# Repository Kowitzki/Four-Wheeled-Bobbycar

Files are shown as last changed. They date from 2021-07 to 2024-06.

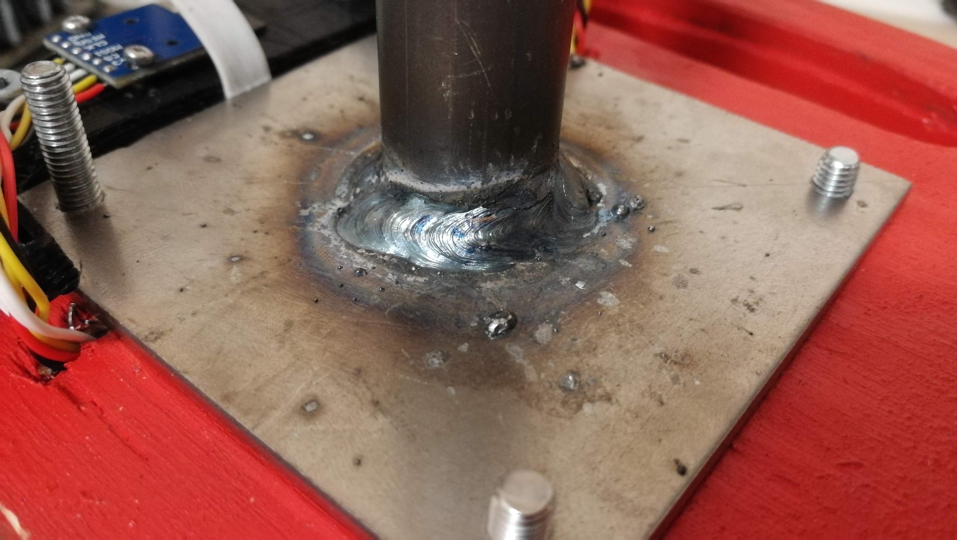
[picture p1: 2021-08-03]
Pictures/IMG_20210313_230046.jpg

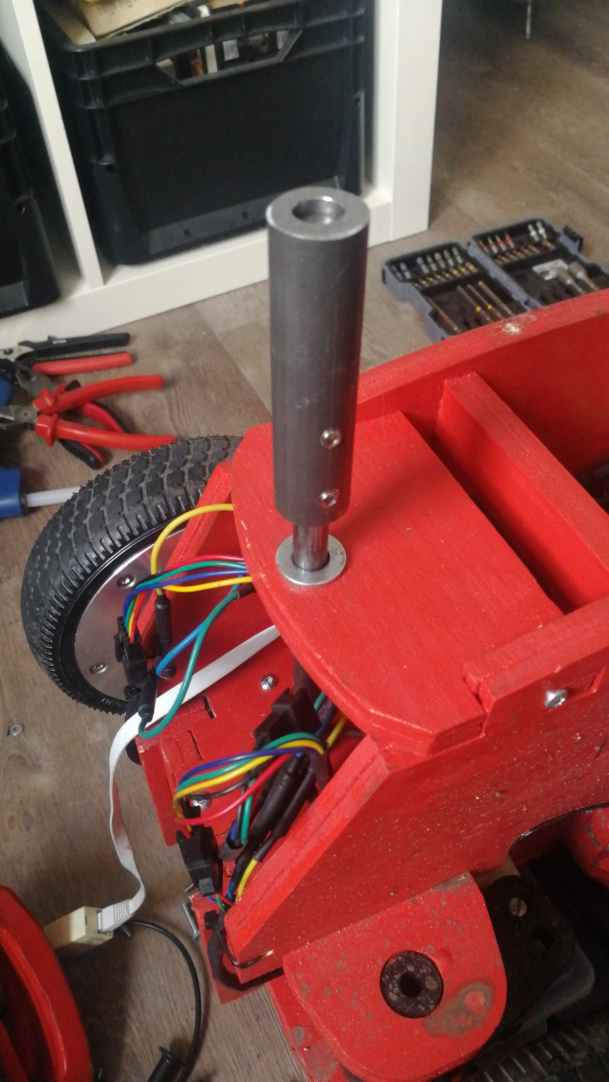
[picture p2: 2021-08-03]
Pictures/IMG-20210312-WA0000.jpeg

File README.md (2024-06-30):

# The black Bobbycar you saw at FSA 2021
There are many possible configurations to built a bobbycar like mine. So you can make changes to any part of this instruction. For example, if you want a better steering, you can change that part. Or if you do not want a Main Controller, you can use the Motorcontrollers directly connected to the potentiometers (throttle and brake).

I recommend to use Hoverboards, you get them used for ~30€ a piece, and they contain almost everything you need. This includes the Motors, which are inside the wheels, the Motorcontroller, which can drive two wheels and the accumulator.
The accumulators are pretty shitty, so not expect them to last very long. In a bobbycar they are overloaded. It helps if you put more of them in there. But you could use other types as well.

The build process gets much easier if you take the rear wheel version instead of the four wheel version. You dont have to weld and you really dont need a seperate main controller. If you are not an electronics or mechanics expert, take the rear wheel version. You find it here: https://github.com/Kowitzki/Rear-Wheeled-Bobbycar  
If you want to build something like this, keep in mind that 3kW is a lot of power and you can harm yourself or others easily. It does not have the safety a formula student car has, so please be careful at testing a new software. I highly recommend to implement a deadman switch, that ensures you really want the motors to spin.

Keep in mind, this is illegal to drive on the street in many countries.

## Software

### Motor Controller
Emanuel Feru wrote a FOC Firmware for the Hoverboard Controllers. This is the one you should flash, but you can also take the original from Niklas Fauth.

Links:
- The used Software for Inverters, took out of Hoverboards https://github.com/EmanuelFeru/hoverboard-firmware-hack-FOC
- The original Software for Inverters, took out of Hoverboards https://github.com/NiklasFauth/hoverboard-firmware-hack

My preferred IDE for the Hoverboard Software is Visual Studio Code with PlatformIO. You have to restart your PC a few times during the installation, that helped me as things did not want to appear as supposed. You can set up the config.h as you like and you can even make changes to the main.c or other files to implement new features. Keep in mind that you should not delete safety features.
Be careful in Torque Mode if you want to get more speed. The MC Software has a bug at high speed. You can drive very fast in field weakening, but then, if you let go the throttle too fast, it brakes really hard. That will not happen if you set the field weakening current in config.h to a normal value like 5-6 Ampere. IF YOU SET IT HIGHER, TELL EVERYONE WHO DRIVES ABOUT THAT ISSUE. 

### Main Control
The Main Controller is programmed by the Arduino IDE with STM32duino. I will upload the software for that but wont go into detail. Maybe i will add some comments.

ST-Link:
You should use a ST-Link V2 for programming the Motor Controllers and the Main Controller.
- ST-Link V2 https://www.ebay.de/sch/i.html?_nkw=st-link+v2&_sop=12
- Virtual COM Port Drivers https://www.st.com/en/development-tools/stsw-stm32102.html

STM32 ST-Link Utility:
From factory the Hoverboard Motorcontrollers are locked, so you have to unlock them by using the STM32 ST-Link Utility and a Flash Device called ST-Link V2. To use the ST-Link you have to install the Virtual COM Port Drivers.
- STM32 ST-Link Utility https://www.st.com/en/development-tools/stsw-link004.html
- How To Unlock https://github.com/EmanuelFeru/hoverboard-firmware-hack-FOC/wiki/How-to-Unlock-MCU-Flash

## Electronics
I would say the electronics of my Bobbycar are pretty advanced, i can control the settings via bluetooth, i have Torque Shifting and a brake light. I would recommend you to not implement those features until it drives. Otherwise you could run into a few problems. These are the parts i used just so this instruction is complete. It would be far easier to take an arduino nano and two potentiometers and flash the arduino code you find in the repository here: https://github.com/EmanuelFeru/hoverboard-firmware-hack-FOC/tree/master/Arduino/hoverserial.

Parts:
- 2x Hoverboards
- 2x 13s eBike Battery with BMS
- Potentiometers out of old XBox360 Controller
- STM32F4 Black Pill (STM32F1 Blue Pill should also work but with another pin configuration)
- Bluetooth HC05
- Display 1602 LCD
- Steering Sensor AS5600
- XL7015 DCDC Converter
- 1x N Mosfet (over 60V V_DS, whatever is lying around, like 110N8F6)
- 1x P Mosfet (over 60V V_SD, whatever is lying around, like IRF9530N)
- 2x Diode
- 2x 10k Resistor
- 1x 50k Resistor
- Port Expander PCF8574A

Schematic for Electronics: https://github.com/Kowitzki/Four-Wheeled-Bobbycar/blob/main/SchematicFourWheel.png

Accumulator
I used two ebike accumulators from aliexpress. They have more voltage than those from Hoverboards, which means a higher speed. Also they have more capacity. Till now they last far better than the original ones.
Two of them have a capacity of about 550Wh, which lasts for 40km at about 20kmh and much coasting without braking.

Links:
- The Schematic of the Hoverboard Controllers https://beta.ivc.no/wiki/images/d/d7/Hoverboard_schematic_full_reverse.pdf
- STM32F4 BlackPill https://docs.zephyrproject.org/latest/boards/arm/blackpill_f411ce/doc/index.html
- STM32F4 BlackPill https://stm32-base.org/boards/STM32F411CEU6-WeAct-Black-Pill-V2.0.html

## Mechanics
The provided CAD Model is built in Autodesk Inventor, but there you can also find a step export.

### Frame
The Frame is built from 6mm and 21mm Plywood (Sperrholz), the kind with long fibres, not pressboard/particle board (Pressspan). Plywood is much more rigid.
There are dxf-files under "Mechanics" for lasercutting. Cutting by Hand is also possible, therefor you need an A3 printer and a jigsaw.
After cutting, 12mm parts are glued together out of 6mm pieces, then everything is pushed together and tightend by screws. Assembling the steering is not that easy, my bad.
If you want your wood to last longer in the rain i recommend you to paint it.

### Steering
The uprights are printed using a 0.8mm or 1mm nozzle, a layer hight of 0.3mm and 60-80% infill. There are two options for the steering, one for normal driving and one for drifting. The options have a different geometry.
Unfortunately the steering shaft has to be welded, but i think every formula student team has someone in their team who can weld. Stick welding is sufficient.
If you use normal structural steel like S235 the steering shaft can be bend easily, already happend twice to me. Maybe you consider getting a tougher steel for the shaft.

# Drift Tires
Yeah, you read it right, i built drift tires for this. Fortunately a pipe in Germany named "Kanalgrundrohr" has the right size for this and is made out of PVC. A slice of this can be glued to printed PLA parts, which are mounted to the hoverboard motors using an TPU adaptor. This has been built, but not been tested yet. I am confident that it will work.

# Formula-Student-Mini
Maybe we can establish a formula competition which is about small, extremely low cost and high powered vehicles. At my University we set up some rules. Some are for safety, some are to harmonize cars and some are for fun.
- Rules https://github.com/Kowitzki/Four-Wheel-Bobbycar/blob/main/Formula%20Student%20Mini%20-%20Rules%20V1.pdf

We have a Telegram Group for the Bobbycars, write a mail for the link

# Known Problems
- The steering is not going back to forward if you let go, and there is much friction. I already thought of putting bearings in there. Also a judge in FSA told me a spring could handle the caster problem.
- The Display is not working on the I2C Line, if the steeringsensor and the port expander for the brake light are used.
- If you have a four wheel car with two MCs, do not drive in field weakening when one controller is off. It would get more voltage than it is supposed to.

# Other Instructions for Bobbycars
- https://larsm.org/allrad-e-bobby-car/
- https://figch.de/index.php?nav=bobbycar

# Safety
- Do not charge unattended
- Do not delete safety features
- Do not drive on public streets
- Use a deadman switch for driving
- Think about what you want to do

# Beer
If you like my effort, i would appreciate if you get me a beer ;)
www.paypal.me/kowitzki/2.00

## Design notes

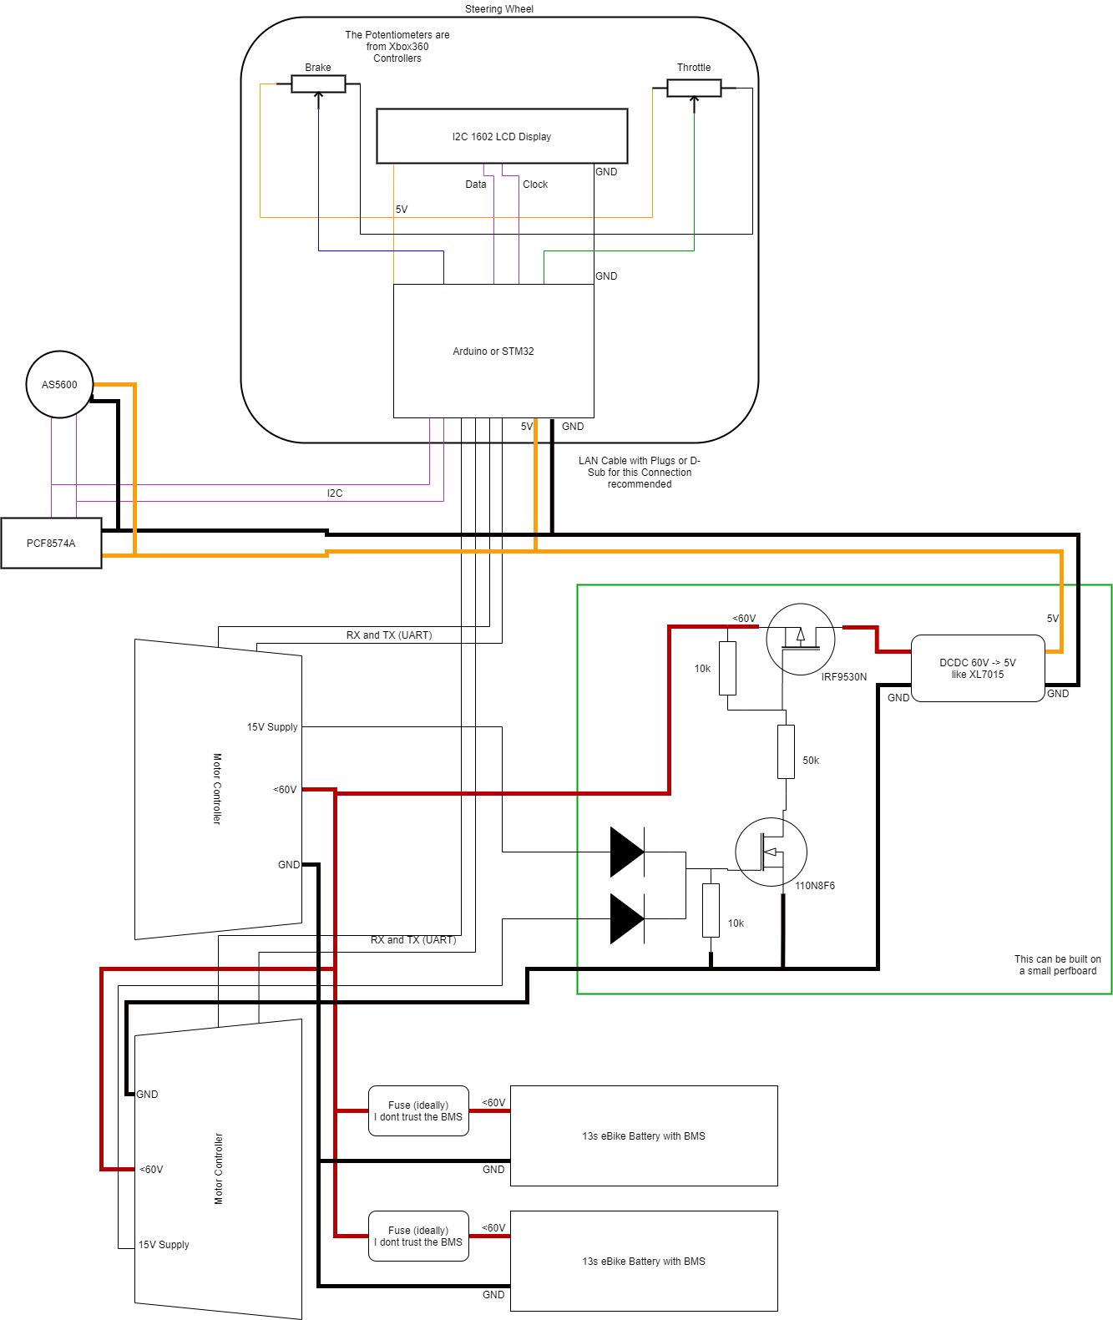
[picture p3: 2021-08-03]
SchematicFourWheel.png

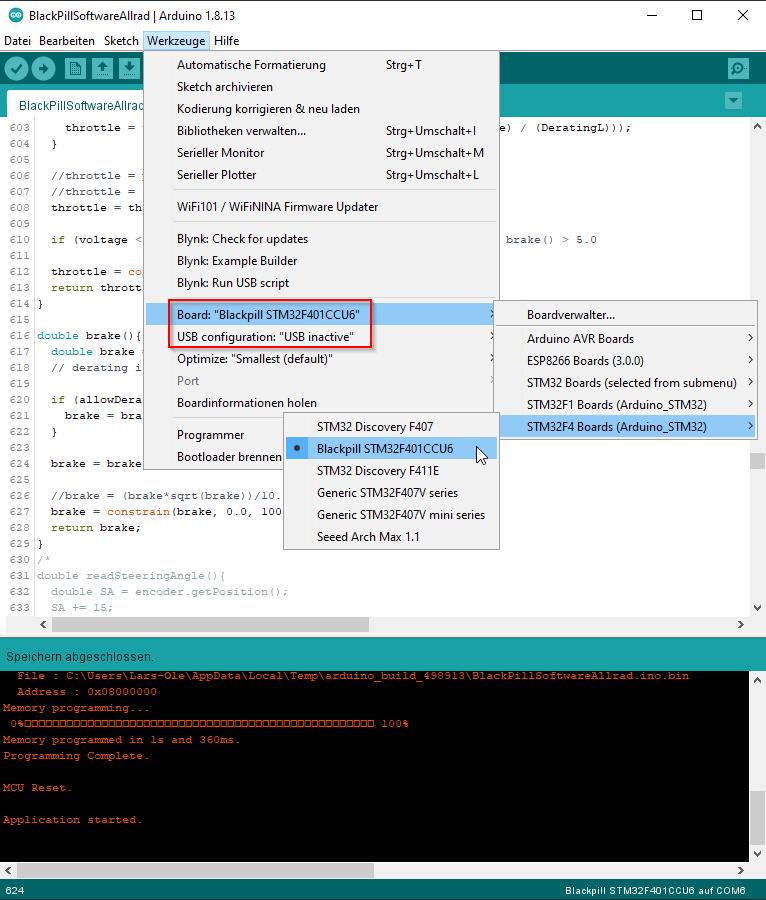
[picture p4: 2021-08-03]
Pictures/STM32_Settings.png

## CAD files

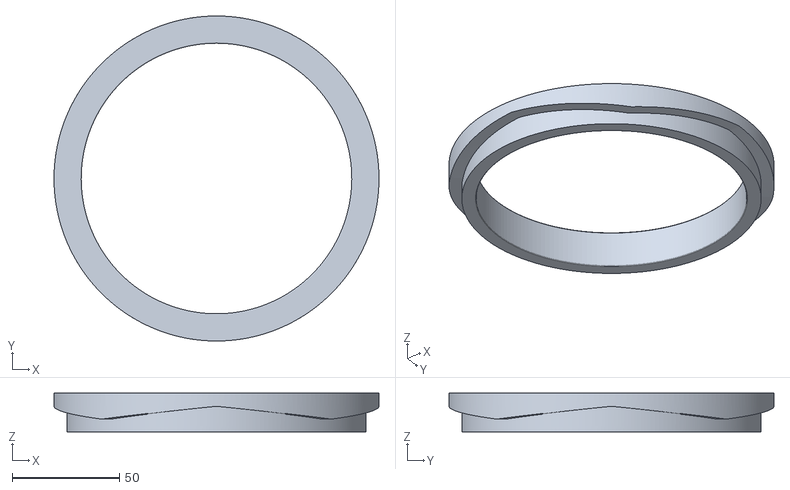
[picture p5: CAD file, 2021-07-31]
DriftreifenTPU/TPU.stl
151.9 x 151.9 x 18.2

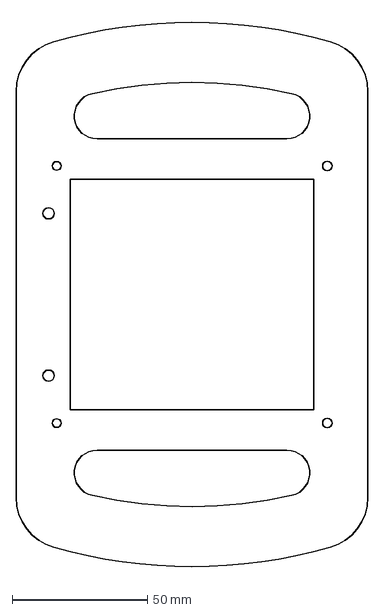
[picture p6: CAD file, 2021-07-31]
DxfWood/LenkradPlatte2.dxf
130.0 x 205.7 mm

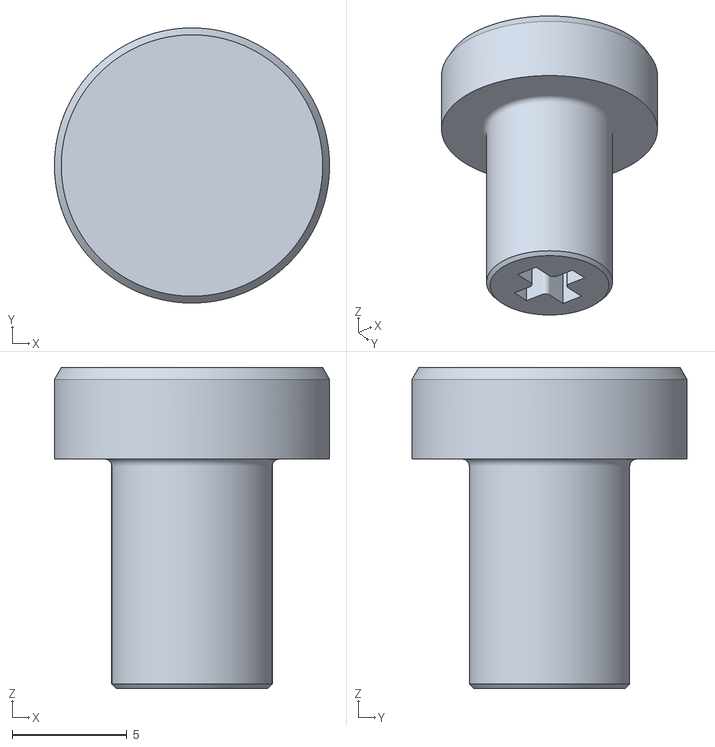
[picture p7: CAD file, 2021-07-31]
Inventor/Totmannknopf.stl
12.0 x 12.0 x 14.0

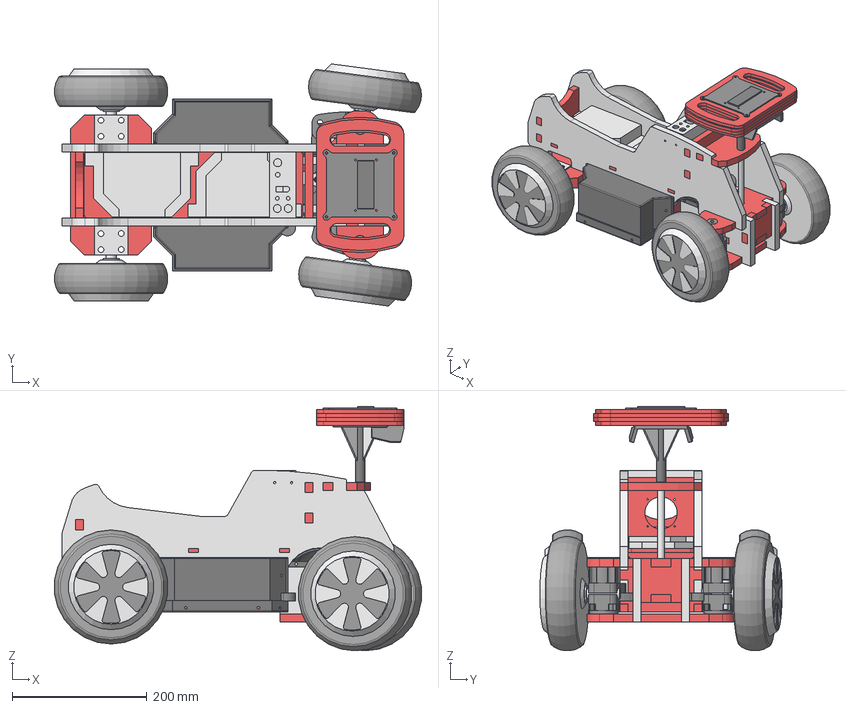
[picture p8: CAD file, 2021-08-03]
MB_BobbyCarAllrad.step
545.3 x 359.9 x 363.2 mm
Kabel
Spannbloecke
Motorplatte
Spannbleche
Haupttraeger
Controllerplatte
Akkubefestigung
QuerstrebeHinten
LenkradStahlplatte
LenkradRohr
LenkradPlatte1
LenkradPlatte2
LenkradPlatte3
LenkradPlatte4
Controller x 2
Akku13s6p
LenkungOben
AkkuSchutz
SeitenträgerInnen
Achsen x 4
Motoren x 4
LenkungUnten
RadträgerL
RadträgerR
Spurstange
SpurstangeGut
Lenkwelle
HalterungLenkwelle
DIN 427 - M8 x 25 x 3
Bodenplatte
XboxTrigger3cuttedScaled
Triggerhalter
Display
LenkradAbdeckung
MCFlashAbdeckung
LenkradStahlVersteifung
RadträgerRUnten
RadträgerLUnten
DIN 7984 - M8 x 40
QuerstrebeVorne
QuerstrebeLenkung
FührungLenkwelle
AkkuSchutzSeitlich
AkkuSchutzSeitlichR
SchutzblechVorneR
SchutzblechVorne
SchalterPanel

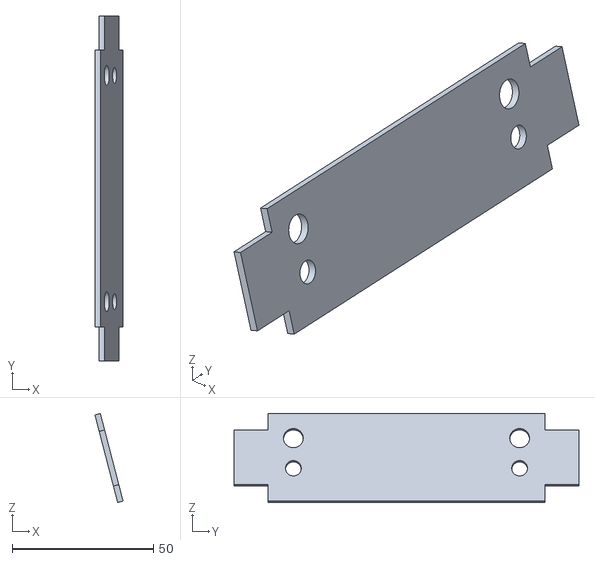
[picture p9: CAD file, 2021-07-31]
PrintedParts/MCFlashAbdeckung.stl
9.98 x 122.0 x 31.5

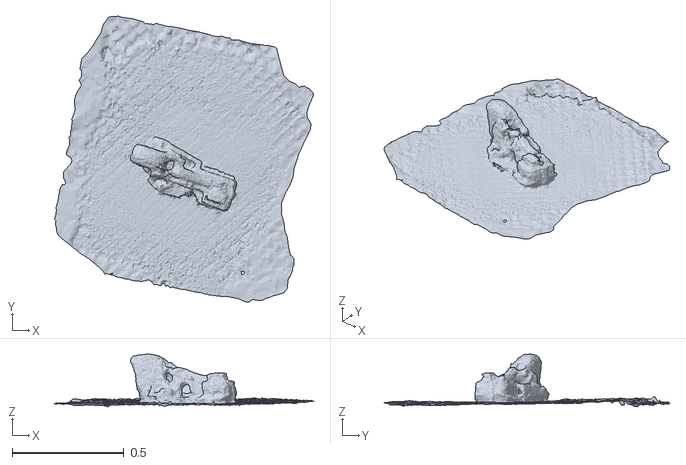
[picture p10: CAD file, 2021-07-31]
XBoxTrigger/XboxTrigger3.stl
1.16 x 1.28 x 0.237

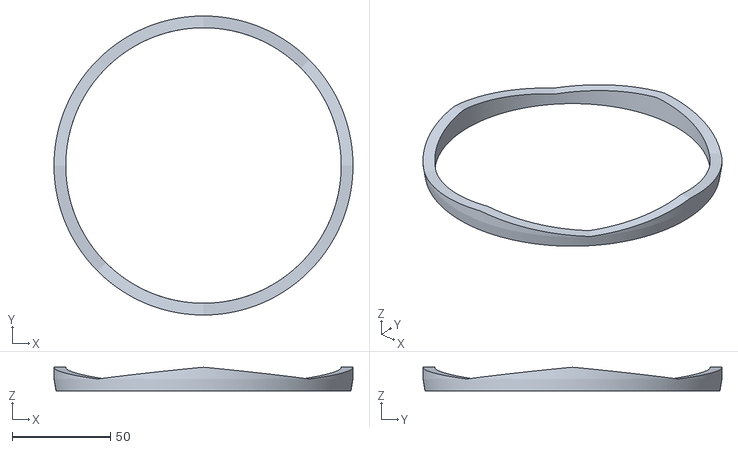
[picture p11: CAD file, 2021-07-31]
DriftreifenTPU/KlebeteiPVC.stl
152.0 x 152.0 x 12.0

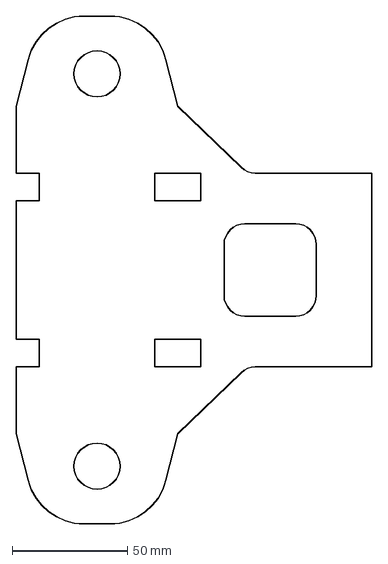
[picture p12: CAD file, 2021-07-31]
DxfWood/LenkungUnten.dxf
154.0 x 220.0 mm

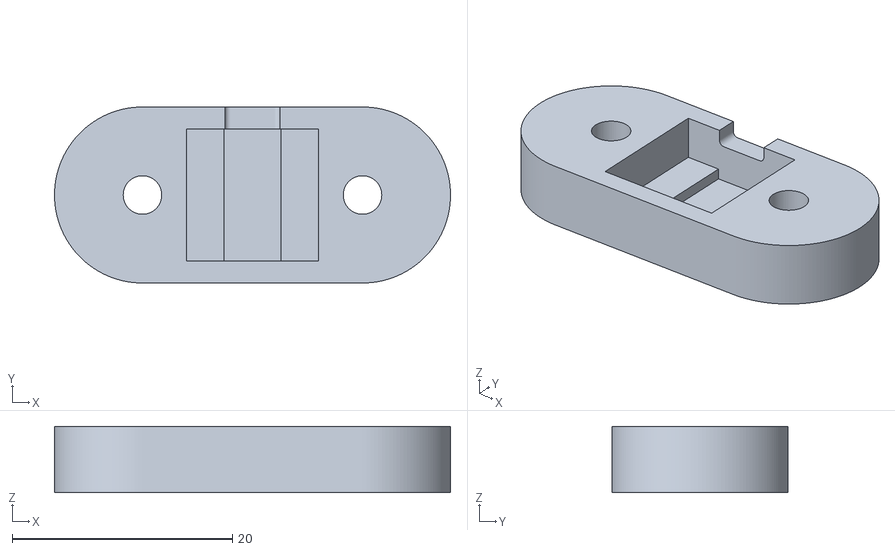
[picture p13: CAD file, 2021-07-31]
Inventor/LenkwinkelsensorAS5600.stl
36.0 x 16.0 x 6.00

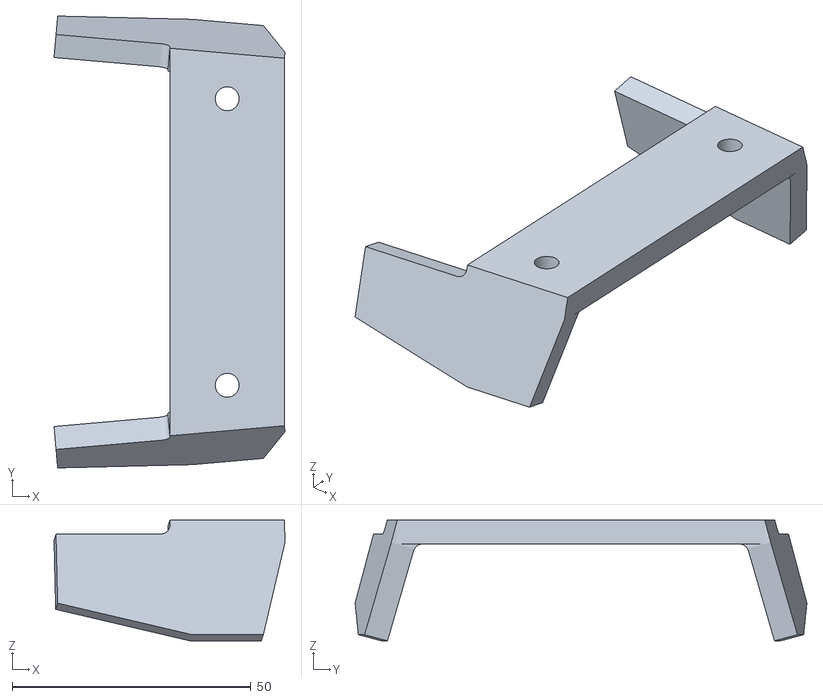
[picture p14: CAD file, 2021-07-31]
PrintedParts/Triggerhalter.stl
48.4 x 94.6 x 25.3

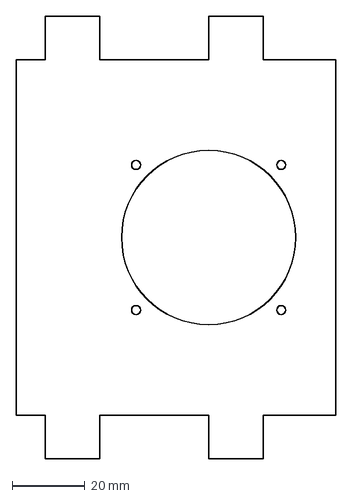
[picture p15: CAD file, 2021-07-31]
DxfWood/QuerstrebeVorne.dxf
88.0 x 122.0 mm

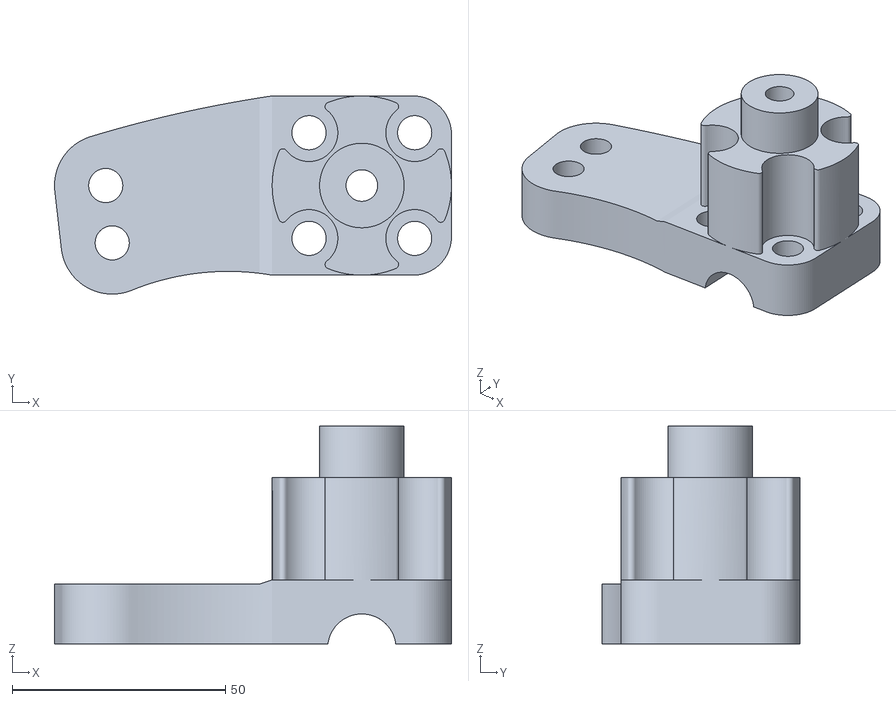
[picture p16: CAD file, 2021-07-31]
PrintedParts/RadträgerL.stl
93.0 x 46.4 x 51.0

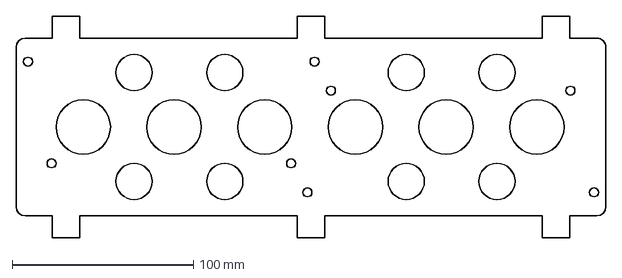
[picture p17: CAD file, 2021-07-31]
DxfWood/Controllerplatte.dxf
325.0 x 122.0 mm

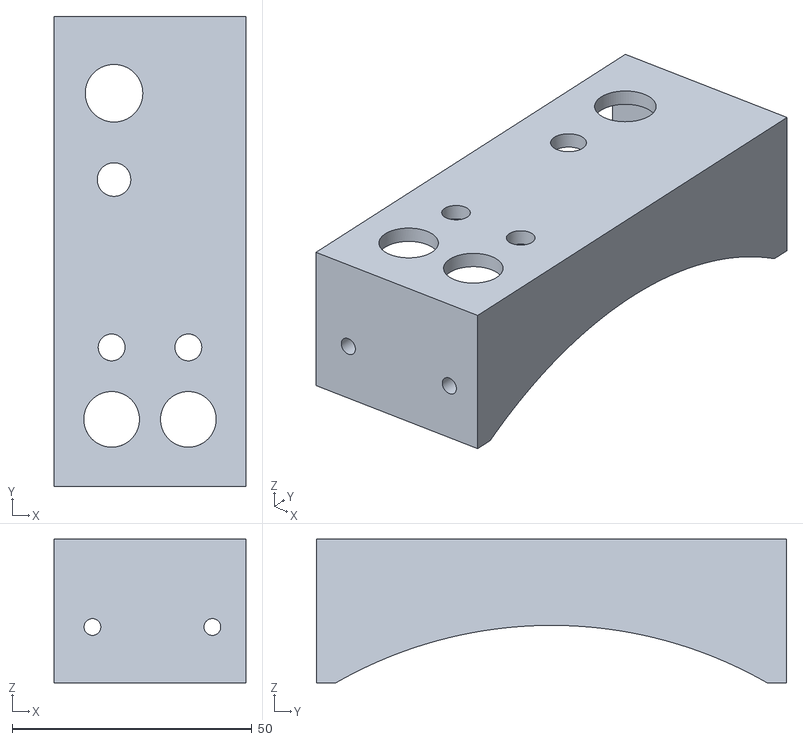
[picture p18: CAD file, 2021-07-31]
PrintedParts/SchalterPanel.stl
40.0 x 98.0 x 30.0

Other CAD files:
DxfWood/SeitentraegerInnen.dxf
PrintedParts/SchutzblechVorne.stl
DxfWood/LenkungOben.dxf
PrintedParts/AkkuSchutzSeitlich.stl
DriftreifenTPU/DriftGummisPVC.iam
DriftreifenTPU/DriftGummisPVC.ipt
DriftreifenTPU/DriftGummisPvcKlebestütze.ipt
DriftreifenTPU/KlebeteiPVC.ipt
DriftreifenTPU/PVC_Adapter.ipt
DriftreifenTPU/PVC_Adapter_Gummi.ipt
DxfWood/AkkuSchutz.dxf
DxfWood/Bodenplatte.dxf
DxfWood/FührungLenkwelle.dxf
DxfWood/HalterungLenkwelle.dxf
DxfWood/Haupttraeger.dxf
DxfWood/LenkradAbdeckung.dxf
DxfWood/LenkradPlatte1.dxf
DxfWood/LenkradPlatte3.dxf
DxfWood/LenkradPlatte4.dxf
DxfWood/MCFlashAbdeckung.dxf
DxfWood/QuerstrebeHinten.dxf
DxfWood/QuerstrebeLenkung.dxf
DxfWood/SpurstangeDrift.dxf
DxfWood/SpurstangeGut.dxf
Inventor/AchseR.ipt
Inventor/Achsen.ipt
Inventor/Akku.ipt
Inventor/Akku10s4p.ipt
Inventor/Akku12s4p.ipt
Inventor/Akku13s3p.ipt
Inventor/Akku13s6p.ipt
Inventor/AkkuSchutz.ipt
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

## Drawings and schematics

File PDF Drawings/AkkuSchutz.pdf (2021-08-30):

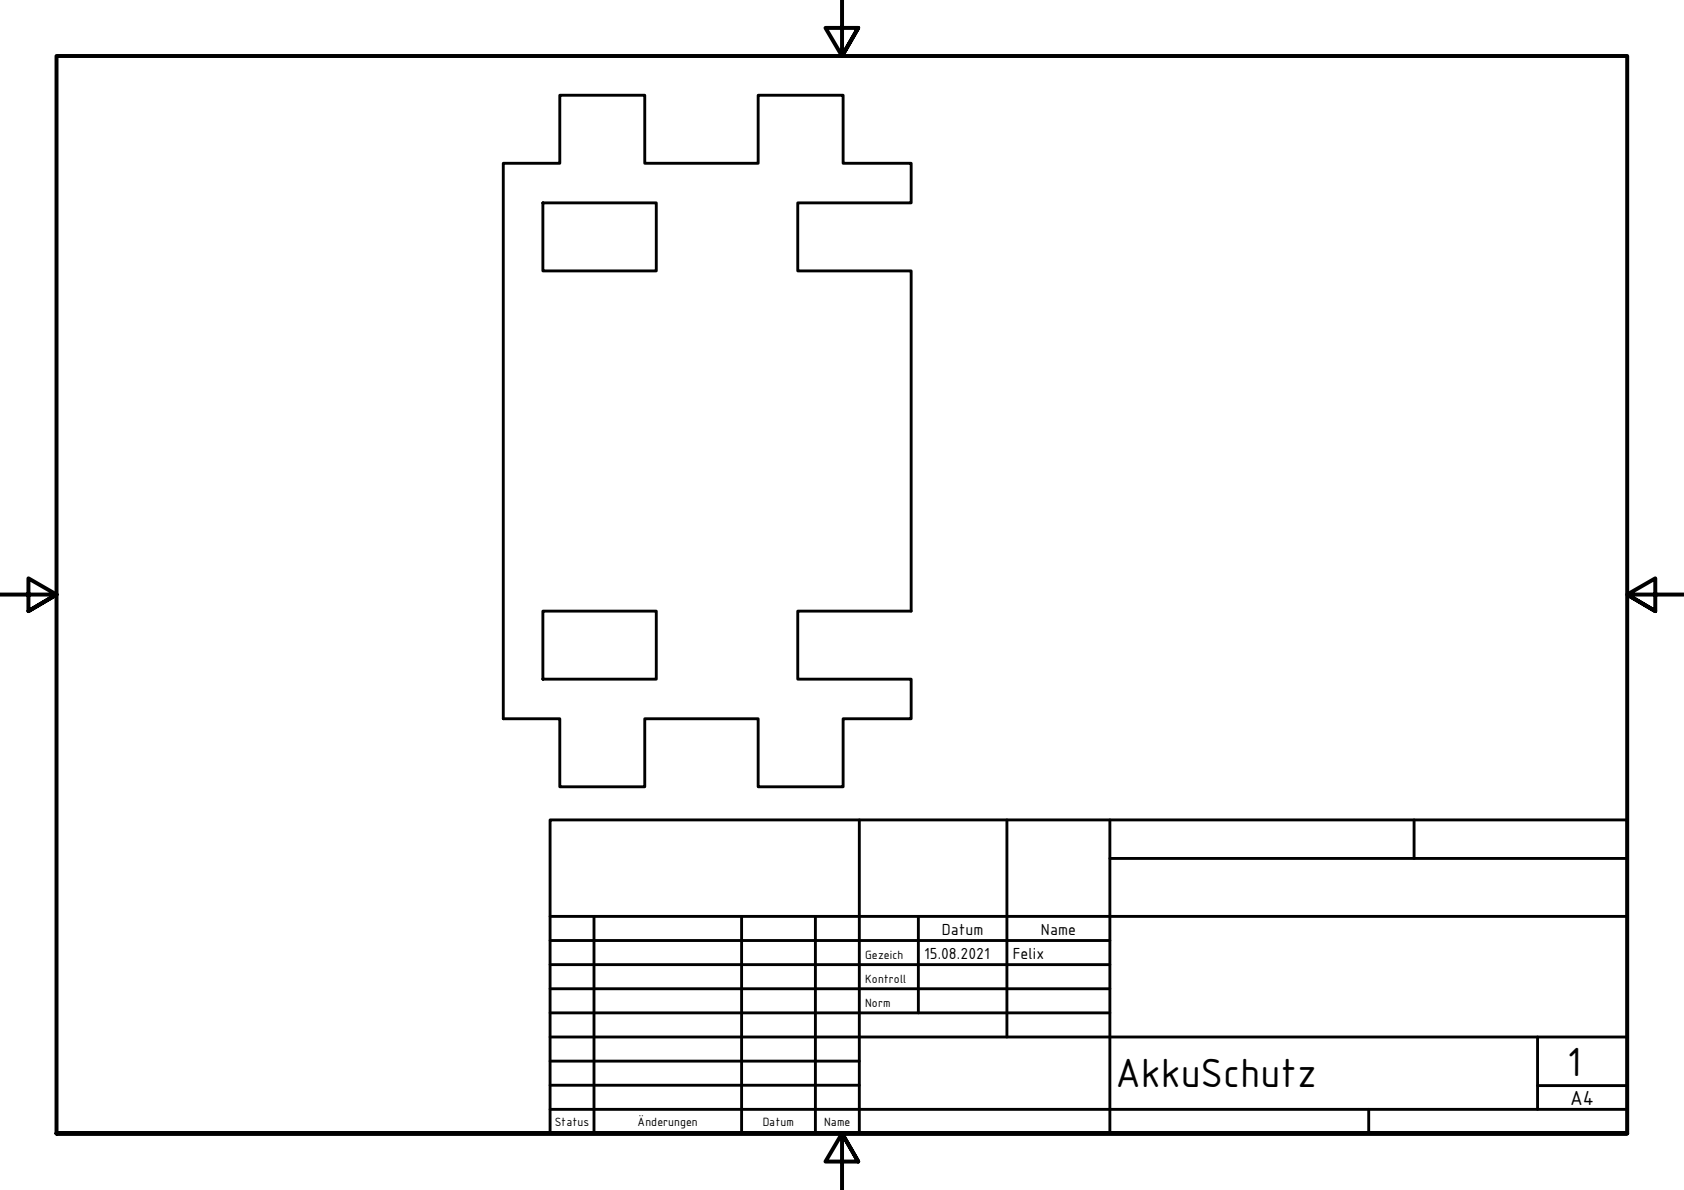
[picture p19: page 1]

G e z eic h | 1 5.0 8.2 0 2 1 | F e lix

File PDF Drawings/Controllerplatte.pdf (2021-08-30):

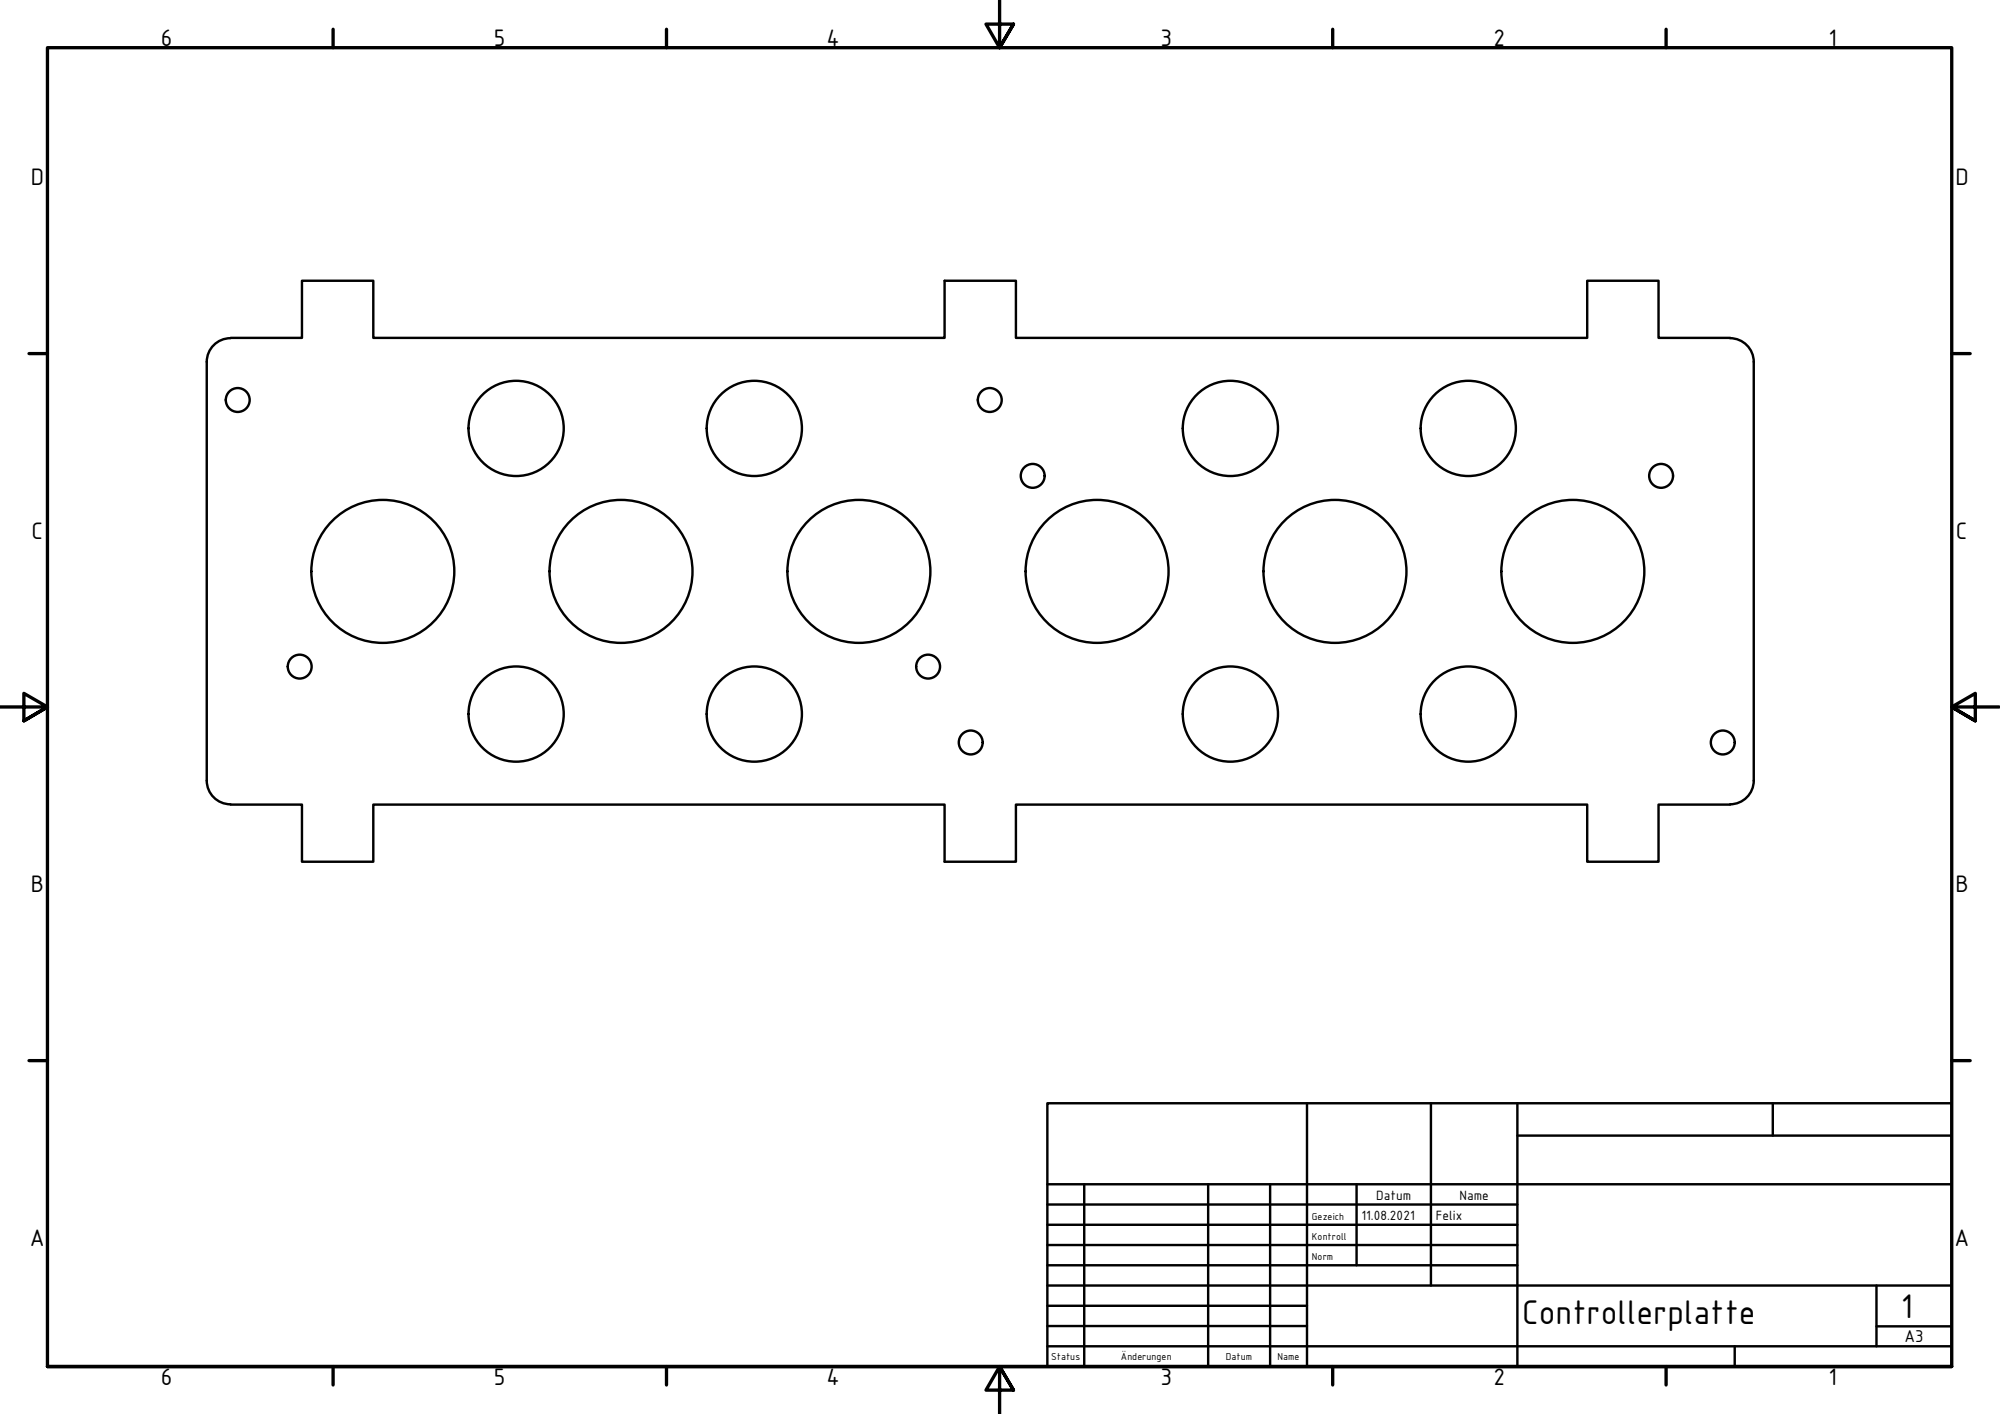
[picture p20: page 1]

Datum | Name

Gezeich | 11.08.2021 | Felix

Kontroll

Norm

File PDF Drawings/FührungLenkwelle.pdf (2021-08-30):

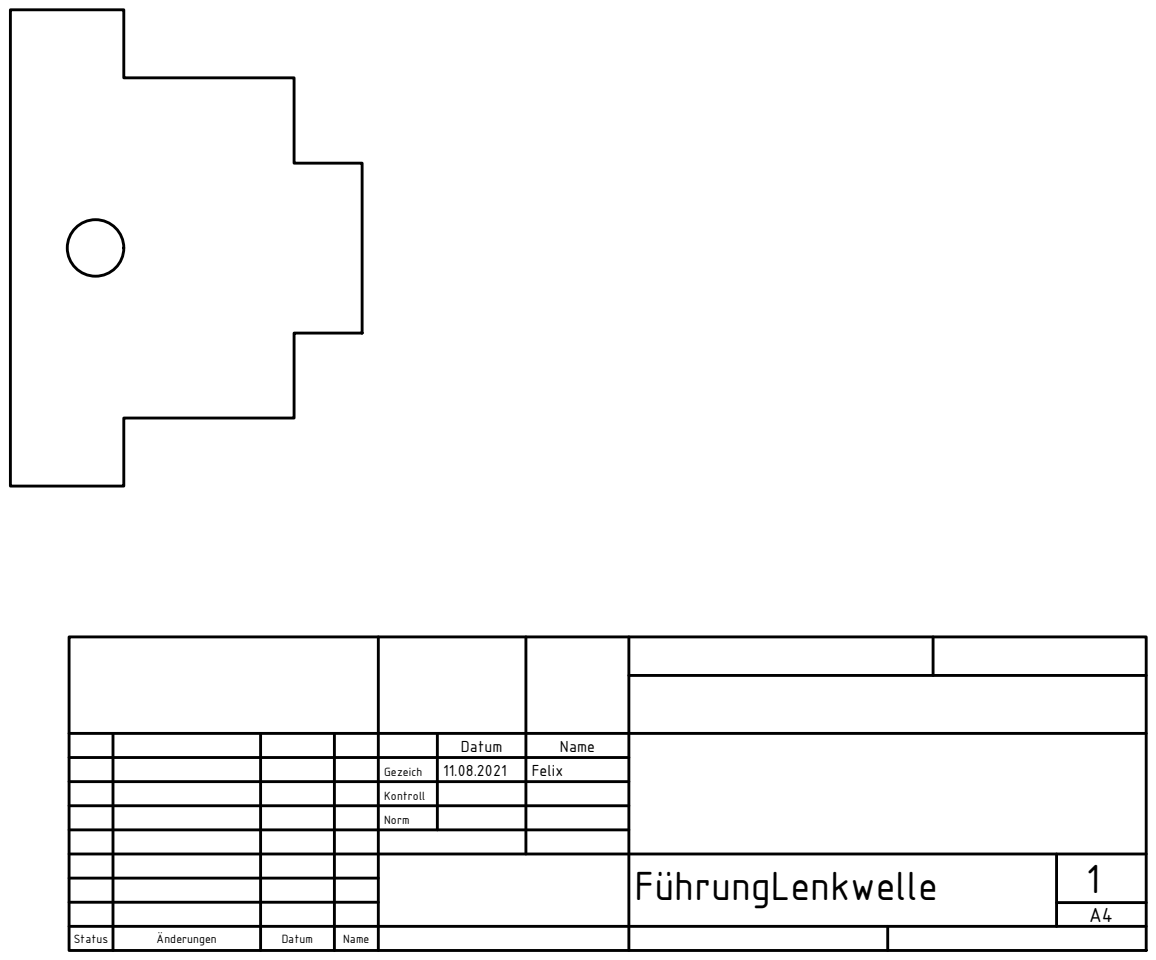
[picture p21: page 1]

G e z eic h | 1 1.0 8.2 0 2 1 | F e lix

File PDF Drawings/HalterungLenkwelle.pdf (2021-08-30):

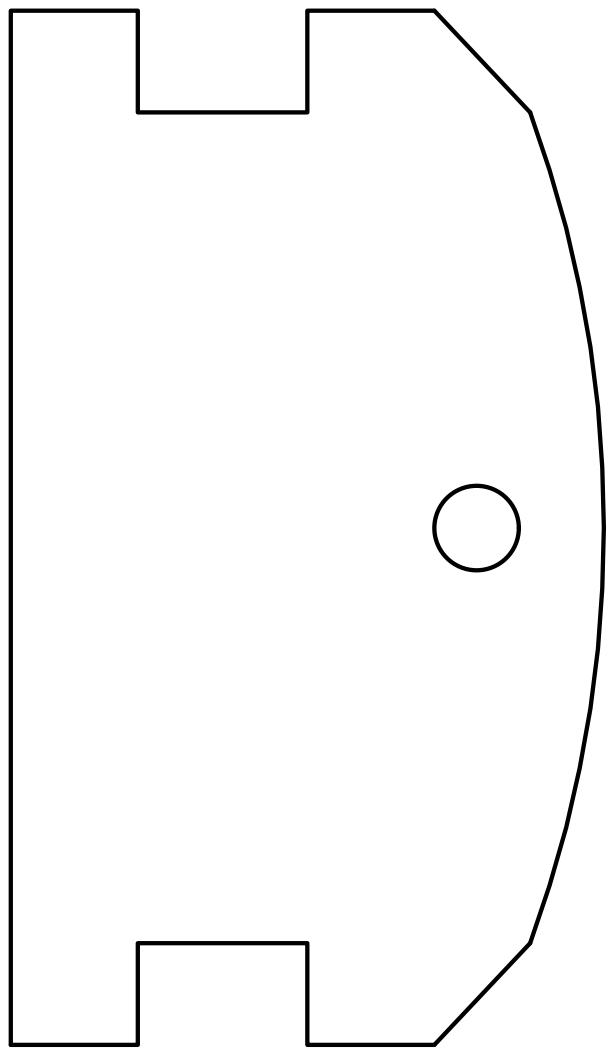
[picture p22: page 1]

G e z eic h | 1 5.0 8.2 0 2 1 | F e lix

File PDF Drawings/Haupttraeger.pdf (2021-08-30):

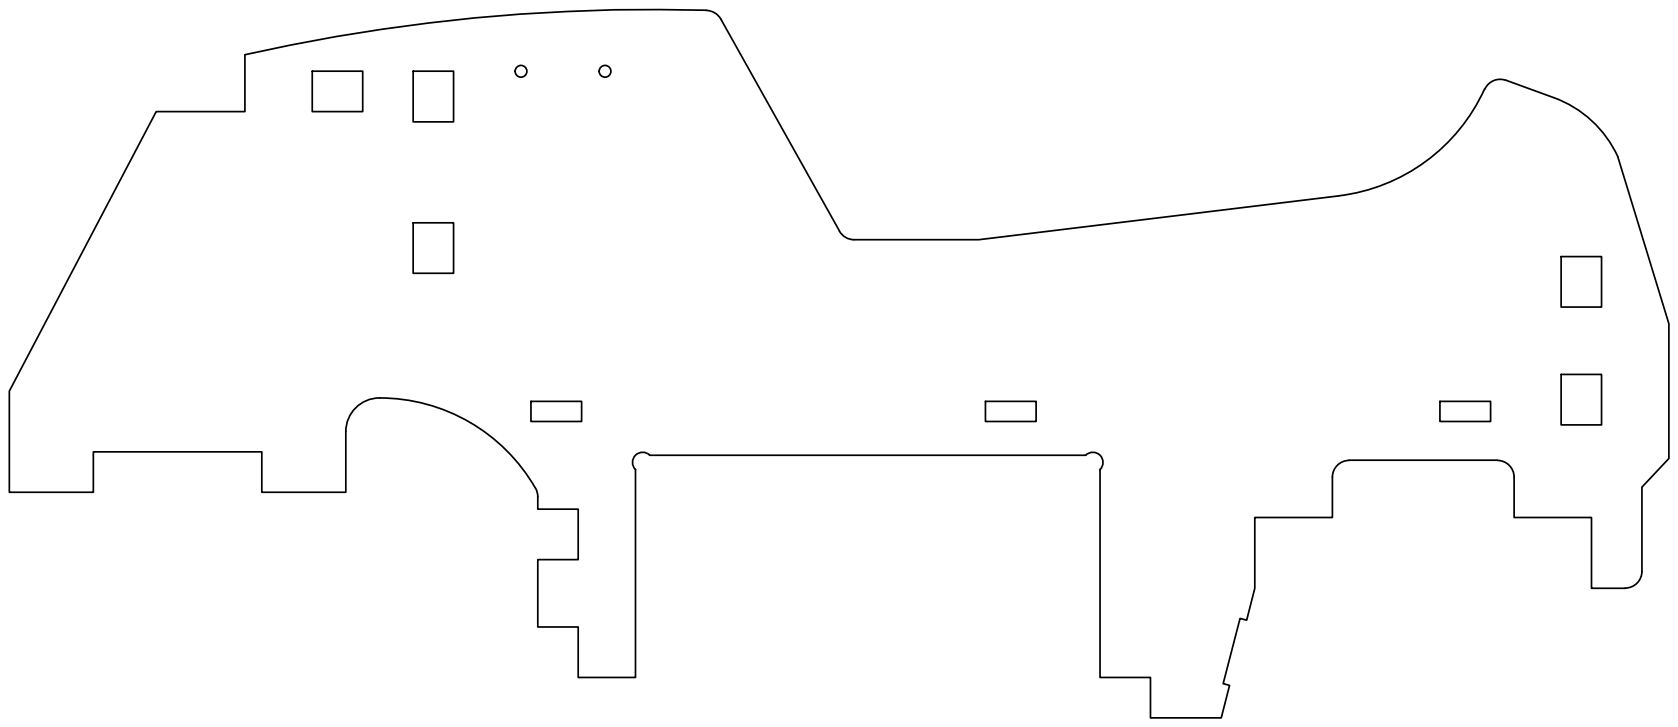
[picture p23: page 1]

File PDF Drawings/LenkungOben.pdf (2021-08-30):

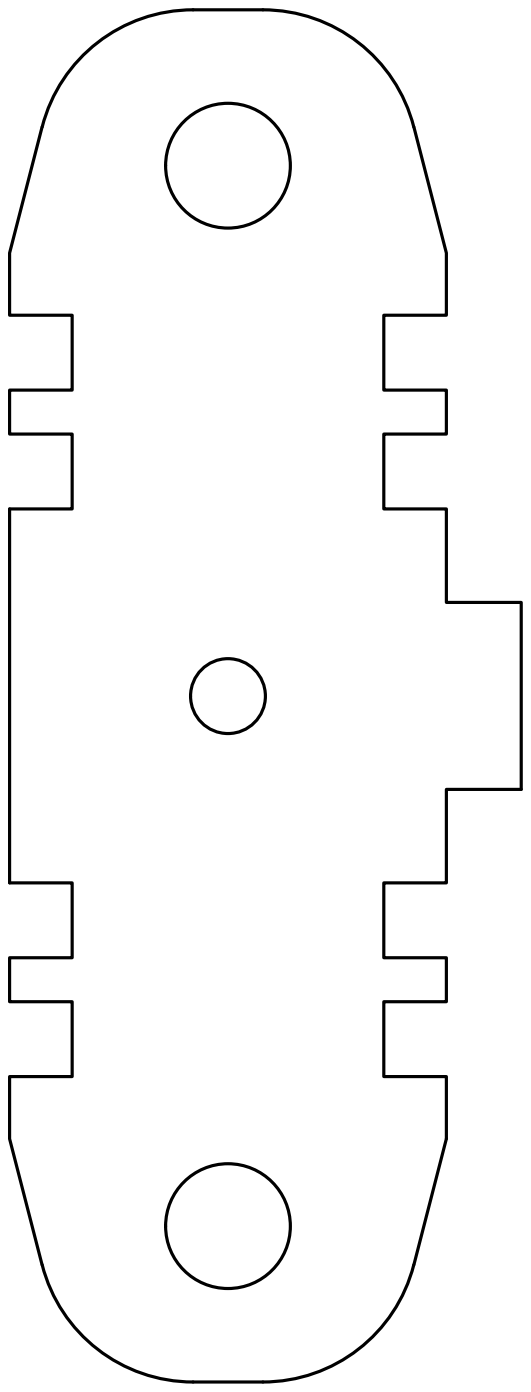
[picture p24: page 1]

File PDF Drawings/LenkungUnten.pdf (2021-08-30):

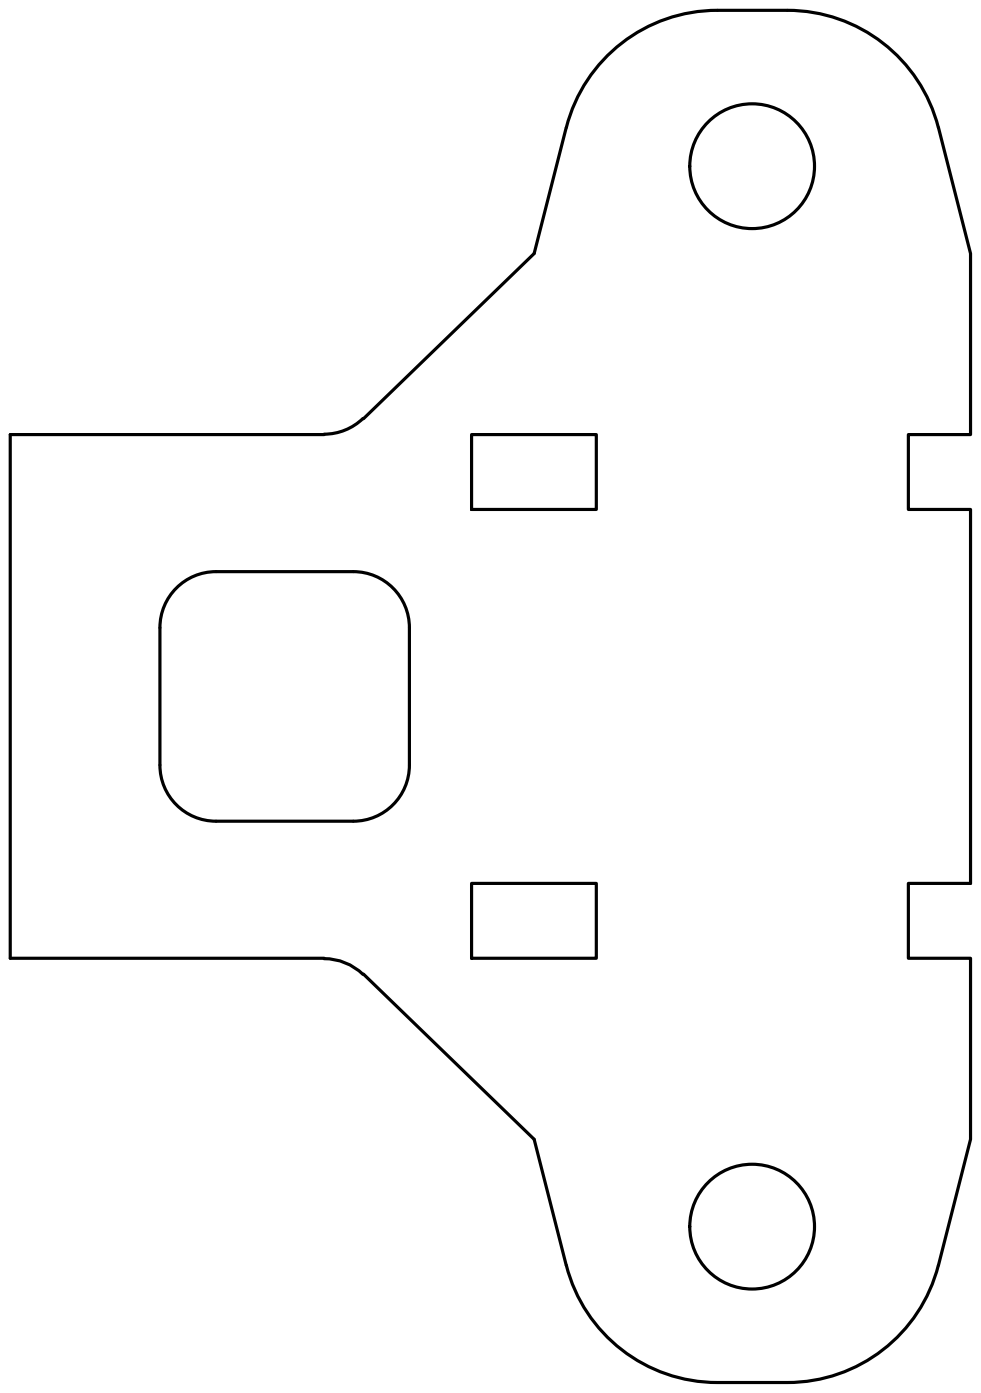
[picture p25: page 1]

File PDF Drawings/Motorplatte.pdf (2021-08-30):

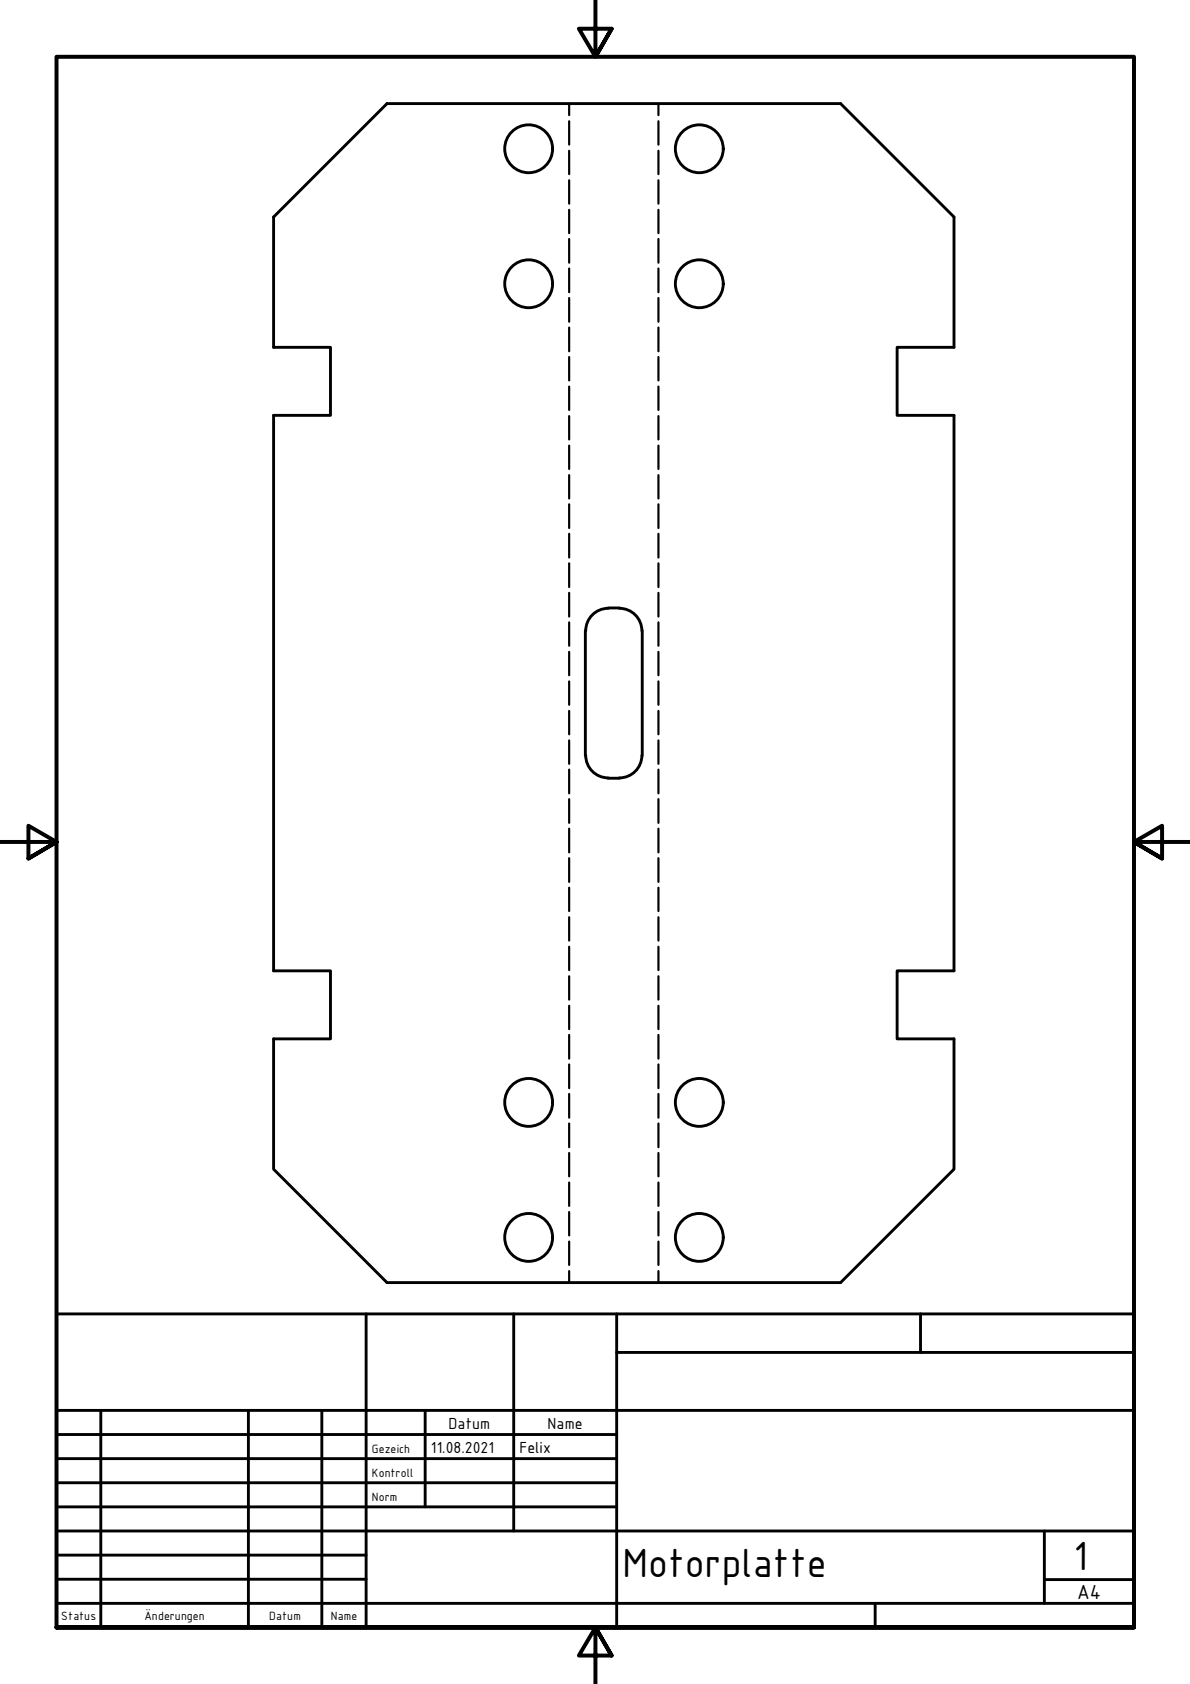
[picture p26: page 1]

G e z eic h | 1 1.0 8.2 0 2 1 | F e lix

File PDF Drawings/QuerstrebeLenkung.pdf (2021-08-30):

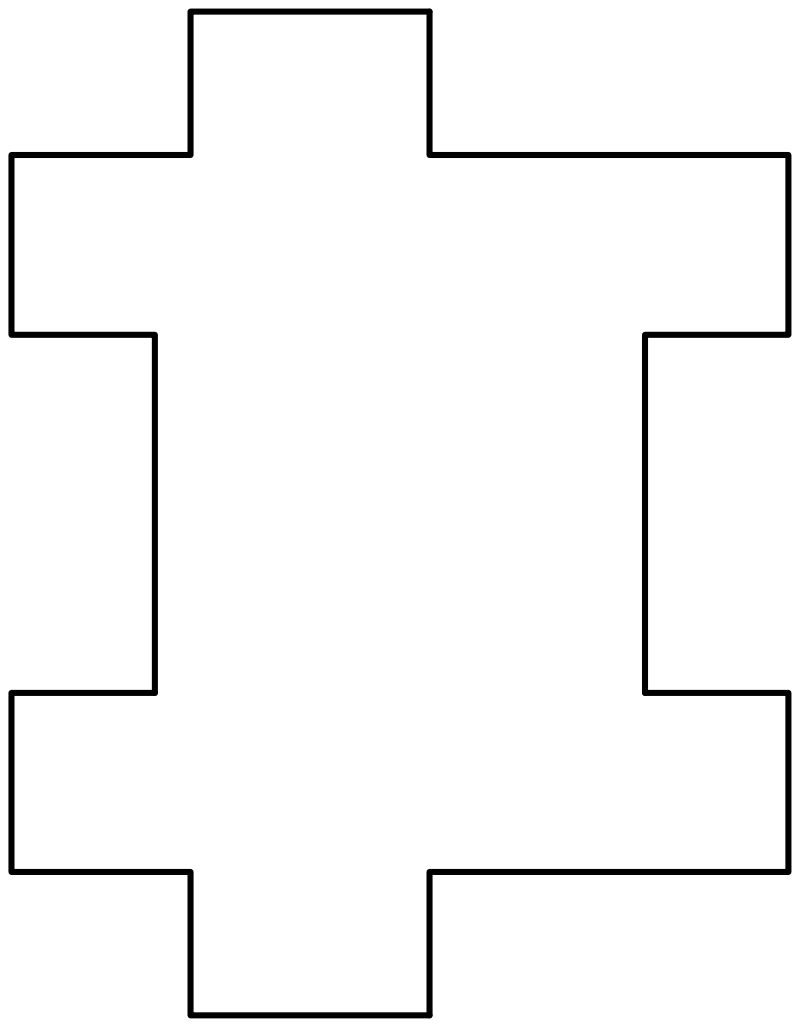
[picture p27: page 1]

G e z eic h | 1 6.0 8.2 0 2 1 | F e lix

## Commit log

2021-07-31 wrong path
    [DriftGummis.iam, DriftGummis.ipt, DriftGummisPVC.iam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]
2021-08-03 added Link to Rear Wheel Version
